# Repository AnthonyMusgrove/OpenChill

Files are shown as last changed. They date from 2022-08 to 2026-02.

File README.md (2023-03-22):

# OpenChill
OpenChill

OpenChill is an open source laser chiller firmware and hardware project using readily available parts from JayCar (Australia)
NOTE: You can also now install OpenChill on an MKS Base v1.4 3D Printer Control Board.  

Updated March 22nd 2023, OpenChill can be installed directly on an ESP8266, wiring diagram & instructions link will be available shortly.  The gist of the implementation is to #define OPENCHILL_ESP8266, set wifi SSID and wifi PASSWORD on lines 183 and 184, and if you want the portal to appear on a static local IP address, you need to #define IS_STATIC_IP then set IP address in segments IP_0,1,2,3, DNS_0,1,2,3, GW_0,1,2,3, and SUBN_0,1,2,3 (lines 191 to 212). You can also change the portal from the default web port 80 by changing #define WEB_PORT 80 (on line 214).

The portal address is simply at http://portal_ip_address<:port (if not 80)> - this will open the basic portal with some simple ajax framework to retrieve the live statistics.   If you just want the JSON statistics feed for your own integrations (into your laser software, etc) simply open http://portal_ip_address<:port (if not 80)>/stats - you'll receive a response similar to:

<code>{"environment":{"temperature": "26.5","humidity": "88","dewpoint": "24.3"},"reservior_temperature":"25.5","fridge_status":"off", "override_status":"off"}</code>

## Why OpenChill?
<p>A Co2 laser tube requires water cooling to maintain power, longevity and safety of the equipment.  The issue is, if the water can't be kept cool enough, the laser starts to lose power and over time, degrades and becomes unusable quicker.</p>  
<p>Why can't we just pump icy cold water through it then using a fridge or freezer?  Well, great question, it turns out that condensation buildup on and inside the laser tube causes 'arcing' and 'shorting' which can be harmful or fatal to YOU, the operator, and your laser.</p><p>  This is where OpenChill comes into play.</p>
<br/>
<p>OpenChill monitors the room's Humidity and Temperature using a sensor connected to the control board.  It then calculates the room's "dew point", which is the temperature in which the tubing will begin to generate condensation. </p><p> The firmware allows you to configure various settings (via wifi/web browser, and eventually a windows app), such as 'Set temperature of chiller dynamic to 3 degrees celsius ABOVE dew point', etcetera.  It will allow for remote monitoring and configuration, and eventually a touch screen, mounts, and more. It will also incorporate the K40 laser 'Cooler Warning' signal wire to shut the laser down incase certain conditions are met.</p>
<br/>
<p>The sky is truly the limit with OpenChill and I can't wait to see the progress over time of this awesome project.</p>
<br/>
<p>Images, instructions, firmware, etc all in progress of ALPHA, once ready for initial commit we can begin group collaboration.</p>

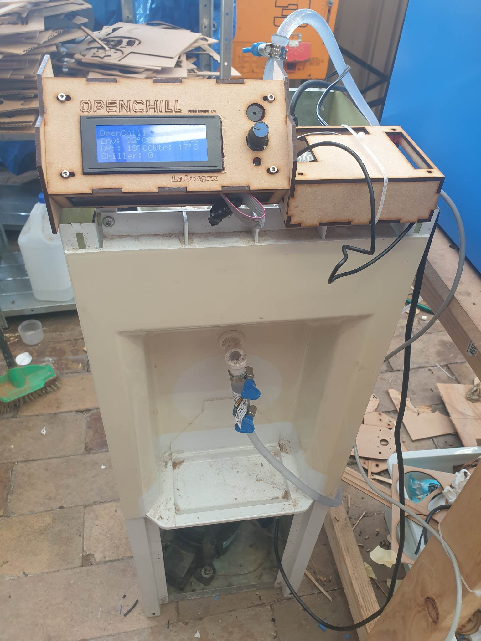
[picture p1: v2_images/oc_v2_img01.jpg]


## Parts List

Please see the BOM and Schematics PDFs -- parts won't be listed here anymore, only in the files.  All parts available from Jaycar Australia

## Non standard bits and pieces

* A water cooler with a working condensor/fridge mechanism.  We will be removing the thermostat that it has and installing OpenChill. 

## Downloads 
* OpenChill Uno Firmware
* OpenChill ESP Firmware
* OpenChill Windows Monitoring Tool
* OpenChill Enclosure Lasercut Files 

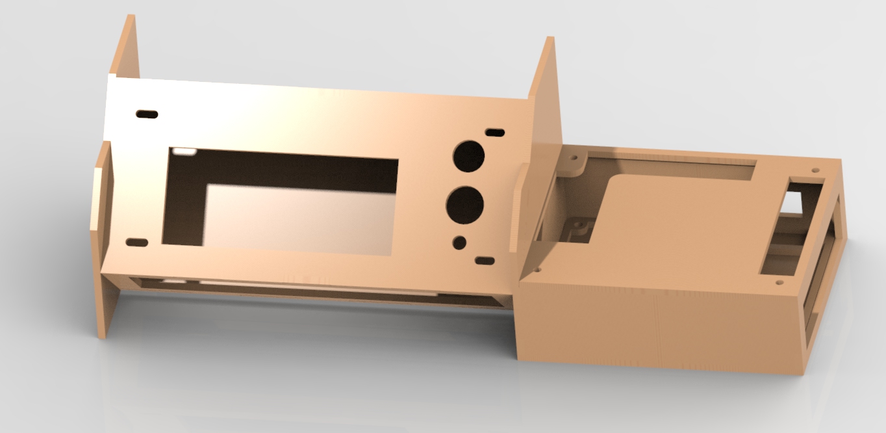
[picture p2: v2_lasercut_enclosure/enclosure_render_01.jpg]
EnclosureRender


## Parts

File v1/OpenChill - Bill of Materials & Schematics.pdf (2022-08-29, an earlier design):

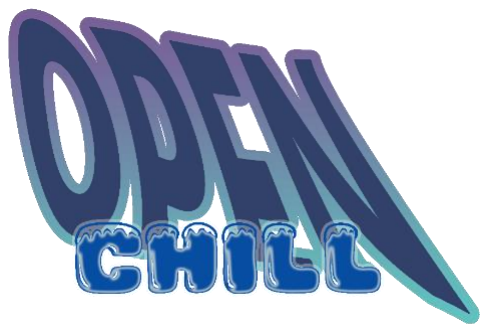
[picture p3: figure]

## Bill of Materials & Schematics

## Ver 1.0.0

## All part numbers refer to Jaycar Part Numbers in Australia; more info: jaycar.com.au

## Anthony Musgrove

## 30th August 2022

## BILL OF MATERIALS

QTY | Part# | Description | Notes
1 | XC4411 | Uno with Wi-Fi | You can substitute this part with a standard Arduino Uno if you don’t want the web portal and remote monitoring
1 | XC4424 | Buzzer Module
1 | XC4520 | Temperature and Humidity Sensor Module
1 | XC4419 | 5V Relay Module
1 | SY4040 | Heavy Duty Chassis Mount 10A /250VAC Relay | https://www.jaycar.com.au/heavy-duty-chassis-mount-relays-30a/p/SY4040
1 | RP7504 | 1k Ohm Linear (B) Single Gang 16mm Potentiometer
1 | RN3440 | 10k NTC Thermistor
1 | PS0524 | Bulkhead Male DC Power Connector
1 | XC4514 | DC Voltage Regulator | Set to 5v for 5v relay & arduino supply (when Arduino isn’t connected to a PC)
10 | HM5172 | 2 Way PCB Screw Terminal | Get spares, they’re useful for interfacing all the bits together

Extras & Notes

Heat shrink & silicone or some other method of waterproofing the 10k NTC Thermistor (it will sit in the chiller water reservoir to measure the chiller’s water temperature). I used some 2mm thick foam and cyanoacrylate (super glue) to make a small envelope around the wiring and thermistor.

The goal is to create a PCB layout and upload so that you can get one made, or make it yourself. This is in the process now, as I’ve now got the schematic and footprints into Altium designer.

The current firmware doesn’t yet utilise the wifi chip on the Uno board – but it will VERY soon. The firmware component for that chip is almost ready to release an alpha version.

Fridge Control Circuit

This is designed to replace the existing thermostat in the water chiller. On the water chillers I’ve looked at, they’re just a two wire thermostat module with two spade terminals. I recommend you getting an electrician to install the main relay (NOT the 5v relay) into the fridge to replace the thermostat – this is important for various reasons and I take absolutely no responsibility whatsoever for any injury, death, damage, or other liability, damage or outcome. You should consult a licenced and qualified electrician for any high voltage side modifications.

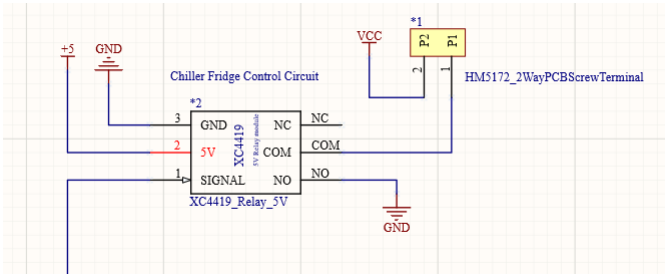
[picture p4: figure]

Signal wire above connects to Digital Pin 8 on the XC4411 Uno with Wi-Fi P1 and P2 need to go to the Fridge Main Relay (250v/10a relay) COIL terminals

Alarm Output Circuit

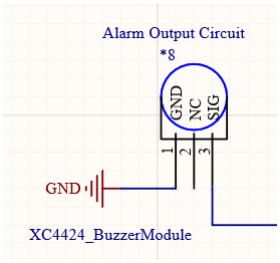
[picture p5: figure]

Pin 3 Signal wire connects to Digital Pin 10 on the XC4411 Uno with Wi-Fi

Environment Temperature & Humidity Input Circuit

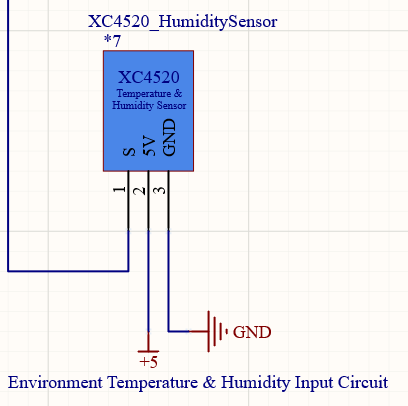
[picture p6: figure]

Pin 1 Signal wire connects to Digital Pin 9 on the XC4411 Uno with Wi-Fi

Chiller Water Temperature Input Circuit

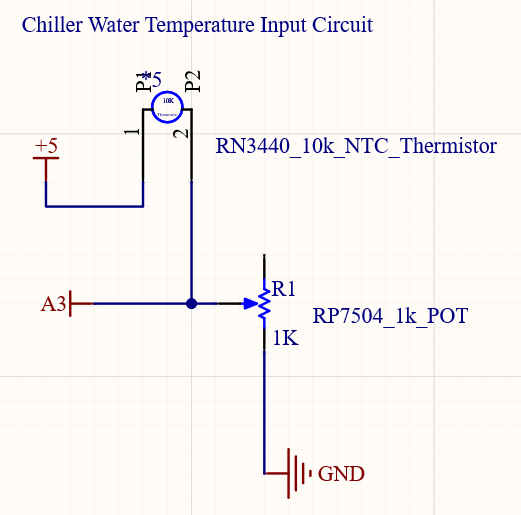
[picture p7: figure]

A3 wire connects to A3 (Analog Pin 3) on the XC4411 Uno with Wi-Fi

Power Supply Circuit

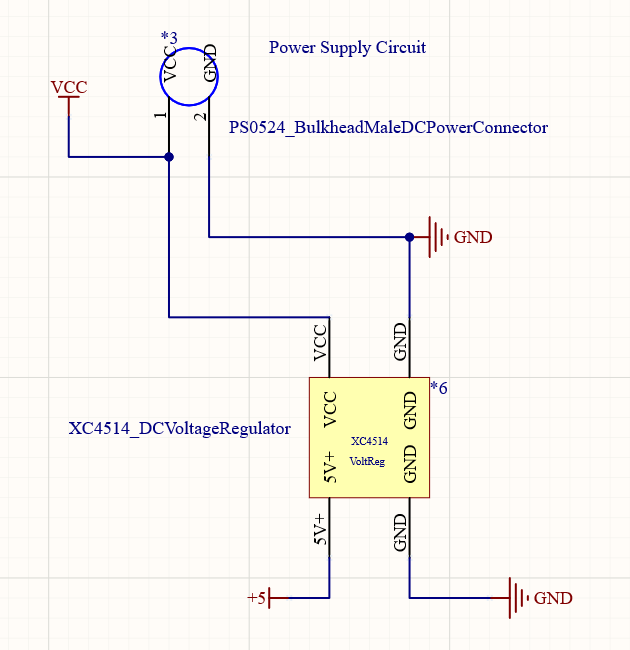
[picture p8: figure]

+5v can go to Arduino VIN to power the Arduino Uno. Make sure GND here is tied to Arduino GND as well. +5v also powers the 5v relay module, and again ensure GND is tied together with ALL grounds in the schematic.

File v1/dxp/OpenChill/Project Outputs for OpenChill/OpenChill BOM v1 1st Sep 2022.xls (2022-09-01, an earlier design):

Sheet: BOM Report
Bill of Materials |  |  | Bill of Materials for Project [OpenChill.PrjPcb] (No PCB Document Selected)
Source Data From: |  | OpenChill.PrjPcb
Project: |  | OpenChill.PrjPcb
Variant: |  | None
Creation Date: | 1/09/2022 | 1:59 PM
Print Date: | 2022-09-01 | 14:00:52
Footprint | Comment | LibRef | Designator | Description | Quantity
OpenChill_2xThruHole | HM5172_2WayPCBScrewTerminal | HM5172_2WayPCBScrewTerminal | *1, *4, *5 | [NoValue], LASER CUTOFF EMERGENCY, LASER ACTIVE | 3
XC4419_5VRelay_Footprint | XC4419_Relay_5V | XC4419_Relay_5V | *2 |  | 1
ARDUINO_INTERFACE_FOOTPRINT | UnoWithWifi | UnoWithWifi | *3 |  | 1
OpenChill_2xThruHole | PS0524_BulkheadMaleDCPowerConnector | PS0524_BulkheadMaleDCPowerConnector | *6 |  | 1
OpenChill_3xThruHole | XC4520_HumiditySensor | XC4520_HumiditySensor | *7 |  | 1
XC4424_BuzzerModule_Footprint | XC4424_BuzzerModule | XC4424_BuzzerModule | *8 |  | 1
OpenChill_2xThruHole | RN3440_10k_NTC_Thermistor | RN3440_10k_NTC_Thermistor | *9 |  | 1
XC4514_VoltReg_Footprint | XC4514_DCVoltageRegulator | XC4514_DCVoltageRegulator | *10 |  | 1
VR5 | RP8510_10k_POT | RPot | R1 | Potentiometer | 1
PARTS NOT LISTED IN SCHEMATIC
SY4040 Relay x1
 |  |  |  |  | 11
Approved |  | Notes

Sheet: Project Information
Project Full Path | C:\Users\Anthony\Documents\GitHub\OpenChill\dxp\OpenChill\OpenChill.PrjPcb
Project Filename | OpenChill.PrjPcb
Variant Name | None
Data-Source Filename | OpenChill.PrjPcb
Data-Source Full Path | C:\Users\Anthony\Documents\GitHub\OpenChill\dxp\OpenChill\OpenChill.PrjPcb
Title | Bill of Materials for Project [OpenChill.PrjPcb] (No PCB Document Selected)
Total Quantity | 11
Report Time | 1:59 PM
Report Date | 1/09/2022
Report Date & Tine | 1/09/2022 1:59 PM
Output Name | Bill of Materials
Output Type | BOM_PartType
Output Generator Name | BOM
Output Generator Description | Bill of Materials

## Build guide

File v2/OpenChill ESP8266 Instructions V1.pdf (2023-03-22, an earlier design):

# ESP8266 Instructions

Document version 1.0.0
Date Released 22/03/2023
Author Anthony Musgrove
Contact anthony@labworx.au

So you’ve heard the great news .. OpenChill can now be installed on a simple mini ESP8266. Well you’ve heard right. Despite the small footprint, the ESP8266 is actually quite a powerful unit, encapsulating WIFI! So the considerations when porting to ESP8266 were that this chip doesn’t have enough pins for an LCD screen with all our other stuff – not a problem, we eliminate that requirement by publishing a simple web portal over wifi so you can monitor OpenChill on your phone or computer, or connect the json data stream directly into compatible software that you can make do with it how you please.

At this stage, the firmware only provides a simple web portal, with statistics output – there’s no configuration changes, etc, so need not worry that it isn’t yet password protected. This can come later.

The other consideration we had to note was the fact that this chip is 3.3v level logic – which means it will NOT switch a 5 volt relay for the compressor – no big issues here though. By far the simplest and most elegant solution here would be to use a solid state relay such as the SSR40 (yeah yeah, 40 amps, a bit overkill Anthony), oh well, they’re cheap as chips – $8-$15 AUD will get you an SSR40 – which gives you the ability to switch up to 40 amps (yes, 40!) at 240volts AC, and will support a switching gate voltage of just 3 volts! Perfect …!

So lets get down to the nitty gritty – this document isn’t yet complete. It’ll be updated after I finish moving house!

Editing the firmware to support ESP8266

First step is to check that the firmware is correctly configured, _before_ you compile it. With the ESP8266, it is a requirement that you set the SSID and Password for your WIFI before compiling and flashing the firmware (at this stage anyway – later we can integrate the settings into the EEPROM and have them modifiable via the web portal – all will come in good time).

First step – define the board name #define OPENCHILL_ESP8266

(this is instead of any of the others, for example OPENCHILL_HARDWARE_V1 or MKS_BASE_1_0).

By defining the board type as OPENCHILL_ESP8266, the firmware will then include and compile the ESP8266 libraries, Wifi client, Webserver and DNS libraries). It will also define the CPU map (pinout wiring) as follows :-

D0 | Unused | Spare (for now)
D1 | Unused | Spare (for now)
D2 | Unused | Spare (for now)
D3 | Override Switch | Input Pullup, switch LOW to activate Override switch – this will keep the fridge compressor ON (or D4 -> HIGH) for as long as the switch is enabled.
D4 | Fridge/Compressor Relay | 3.3v output logic for the Solid State Relay gate
D5 | Buzzer/Audio | For alerts/alarms. If you don’t add a buzzer, no big deal – you just won’t hear it if it detects the reservoir temperature above the maximum allowed value
D6 | Safety Cutoff Signal | Not yet used – will be soon
D7 | Laser In Use Signal | Not yet used – will be soon
D8 | DHT11/22/etc Sensor Signal | The (S)ignal pin from your DHT11 or DHT22 sensor
A0 | Reservoir Temperature Signal | Analog Input pin for a temperature probe – I made my probe from a simple thermocouple in heatshrink then covered in foam. Depending on your thermocouple you use you may need to change the mapping code manually to support its range – we need to make this more versatile in the future

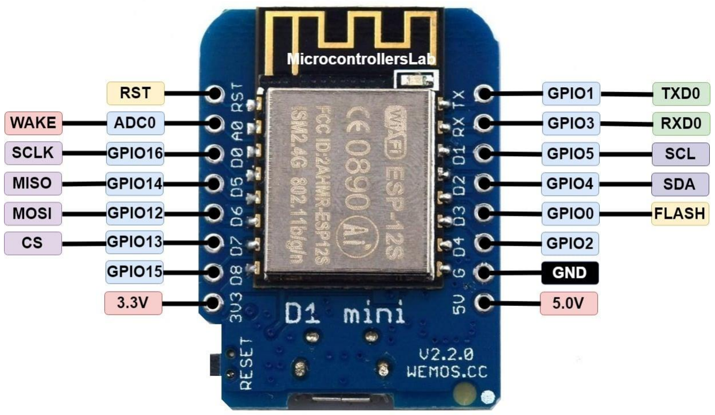
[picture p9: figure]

You need to configure your wifi SSID and PASSWORD. If you’re unsure of these values they may be on a sticker on your router.

Scroll down to line 183 (approx.) and configure the following lines :-

#define WIFI_SSID | "YourWIFISSIDHere"

#define WIFI_PASSWD | "YourWIFIPasswordHere"

Along with configuring the wifi SSID and PASSWORD – you can also specify a static lan IP address if you wish to have the web portal / json data stream open on the same IP address always – you can also override the default web port 80.

To set a static IP

Scroll down to line 186 (approx.) of the firmware and find the line

#define IS_STATIC_IP

Once you’ve told OpenChill firmware to use a static IP, you need to set the values from approx. line 191 to line 212. They include IP, DNS, Gateway and Subnet Mask, example shown below:

/* Portal IP Address (Example: 192.168.1.75) */
#define IP_0 192

#define IP_1 168

#define IP_2 1

#define IP_3 85

/* DNS IP Address (Example: 192.168.1.1) */ #define DNS_0 192
#define DNS_1 168

#define DNS_2 1

#define DNS_3 1

/* Gateway/Router Address (Example: 192.168.1.1) */ #define GW_0 192
#define GW_1 168

#define GW_2 1

#define GW_3 1

/* Subnet Mask (Example: 255.255.255.0) */ #define SUBN_0 255
#define SUBN_1 255

#define SUBN_2 255

#define SUBN_3 0

This will tell the firmware to publish the simple web portal on IP address 192.168.1.85, using DNS server 192.168.1.1, Gateway (or your wifi router address) 192.168.1.1, and a subnet mask of 255.255.255.0 – networking configuration is out of scope for this document – If you need to clarify any of these settings you need to either speak with your network administrator or read up on your router settings (and local area network settings). Who knows, we might do some more in depth tutorials on this stuff at a later stage.

Changing the default port for the portal

If you want to take the portal off the default web (http) port (80), you can modify the line (approx. 214):

#define WEB_PORT | 80

Once you’ve got your settings modified, compile the firmware using the Arduino IDE, while your ESP8266 is connected via USB (or however you wish to achieve programming your ESP8266).

When you boot it up, you should see a simple web portal on your portal address :

http://static_configured_ip:port

Note – if your port is left at default 80, you do not need to specify a port, simply http://ip_address/

Also note – if you did not choose to use a static IP address, you’ll need to locate the device on your local network by either IP scanning your net range, or checking ‘connected devices’ or the like on your wifi router/modem.

The simple portal appears somewhat like the following :-

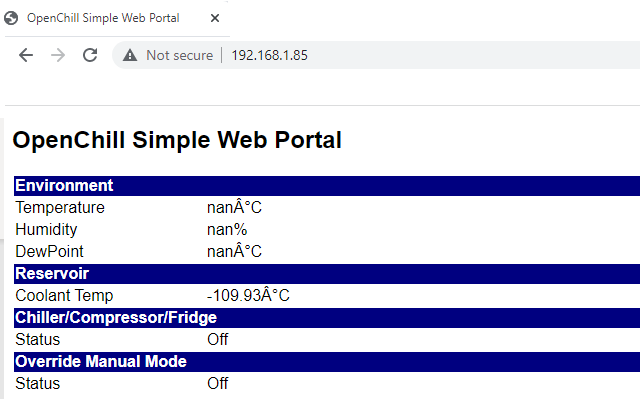
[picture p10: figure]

Environment Temperature and Humidity come from your DHT11/22 sensor. The dewpoint is calculated using the dewpoint formula (Td = T 0((100 -RH/5.) where Td is dew point temperature (in degrees Celsius), T is observed temperature (in degrees Celsius), and RH is relative humidity (in percent).

The values shown in my example above are what you’ll typically see without your DHT11/22 sensor connected (nan = Not A Number), and the firmware knows not to attempt to switch on the compressor if these invalid values are received).

Reservoir Coolant Temperature is the temperature value received by your temperature probe installed inside your chiller – remember this may be inaccurate and may need calibrating (and even some code changes to the mapping etc) – right now this isn’t very versatile so this is a massive TODO for the near future – to get some predefined sensor types and their mapping values into the firmware. For now though, use a BBQ probe or Meat probe and do some calculations to getting your particular sensor working correctly.

Chiller/Compressor/Fridge Status is the indicative value that your logic gate for your solid state relay is ON or OFF – and this subsequently will be what powers your compressor pump or whatever you choose to power with the solid state relay.

Override Manual Mode Status is the status of your manual override switch. If you choose to use a manual override switch – I added it as I found it handy when my temperature probe is inaccurate (because of calibration issues) and I really needed to get laser jobs done, I’d just flick it over to manual mode and monitor the temperature manually – however I rarely need this now as I’ve got my implementation configured/dialed in pretty well.

How do I just access the raw stats?

If you just want a JSON formatted feed of the vitals from openchill, such that you can connect it to your laser software or some other software that can use this data, etc, you can open the stats URL directly at:

http://openchill_ip_address/stats (if you changed your default web port from 80, you’ll also need to specify the port – ie: http://openchill_ip_address:port/stats).

You’ll be presented with the JSON formatted stats data which will appear like the following -:

{"environment":
{"temperature": "nan",
"humidity": "nan",
"dewpoint": "nan"},
"reservior_temperature":"-109.93", "fridge_status":"Off",
"override_status":"Off"}

When you have sensors connected and its working correctly, you’ll see values instead of nan (not a number) for temperature, humidity and dewpoint.

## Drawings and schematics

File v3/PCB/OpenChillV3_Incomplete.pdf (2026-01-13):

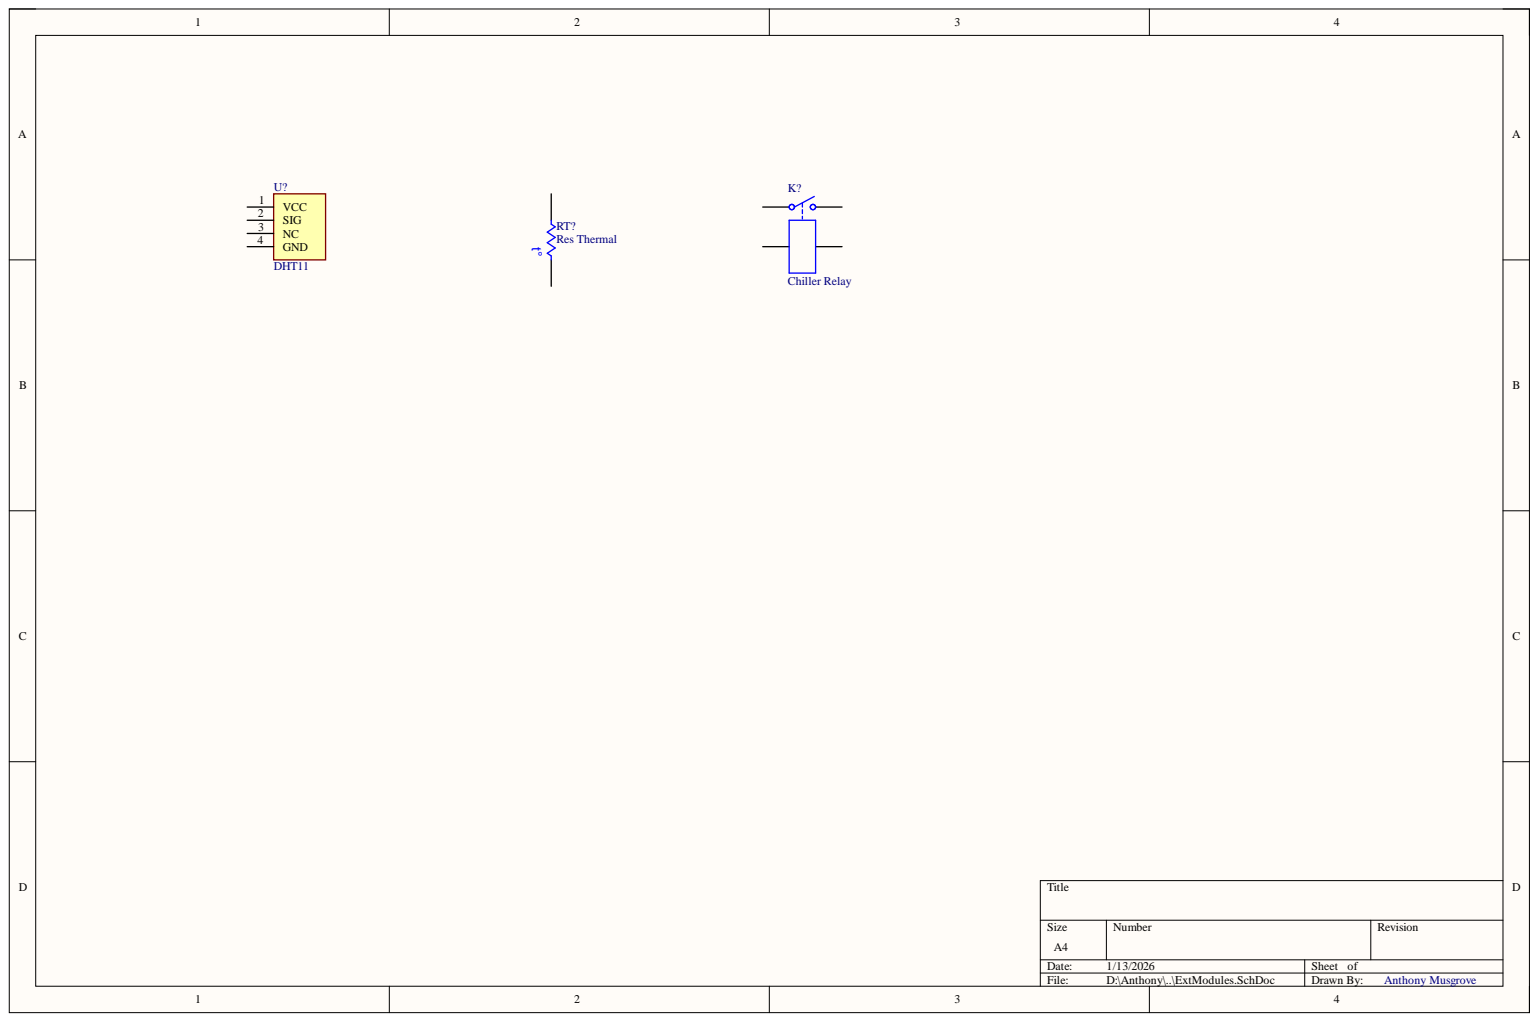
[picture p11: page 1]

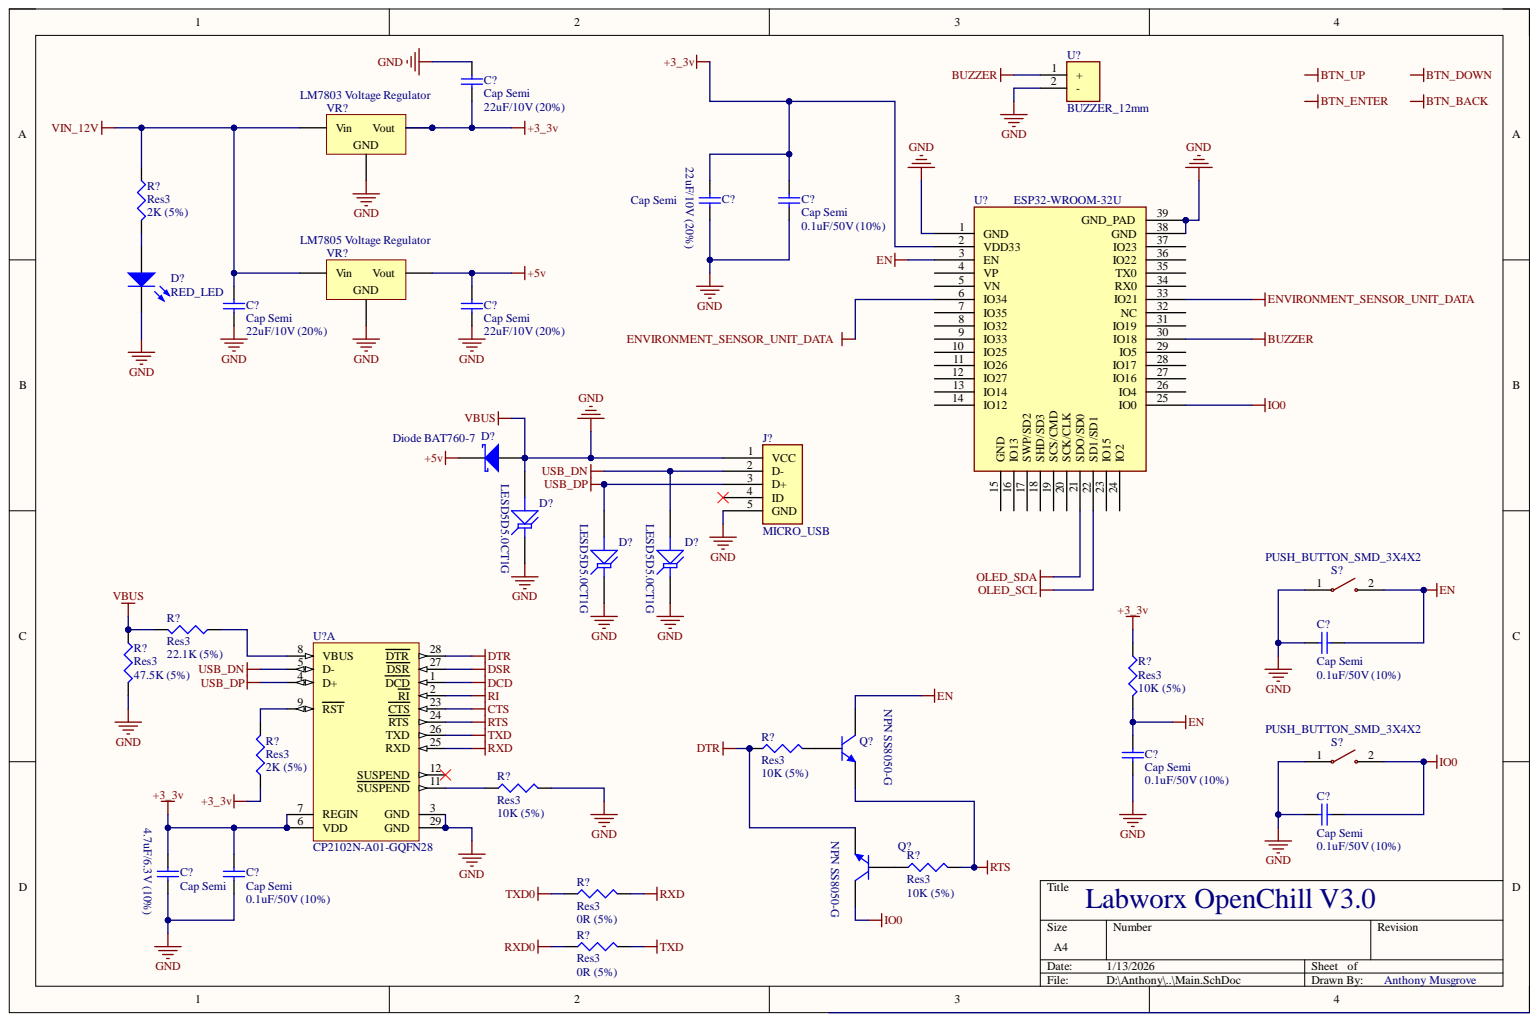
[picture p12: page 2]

D- 2
D+ 3

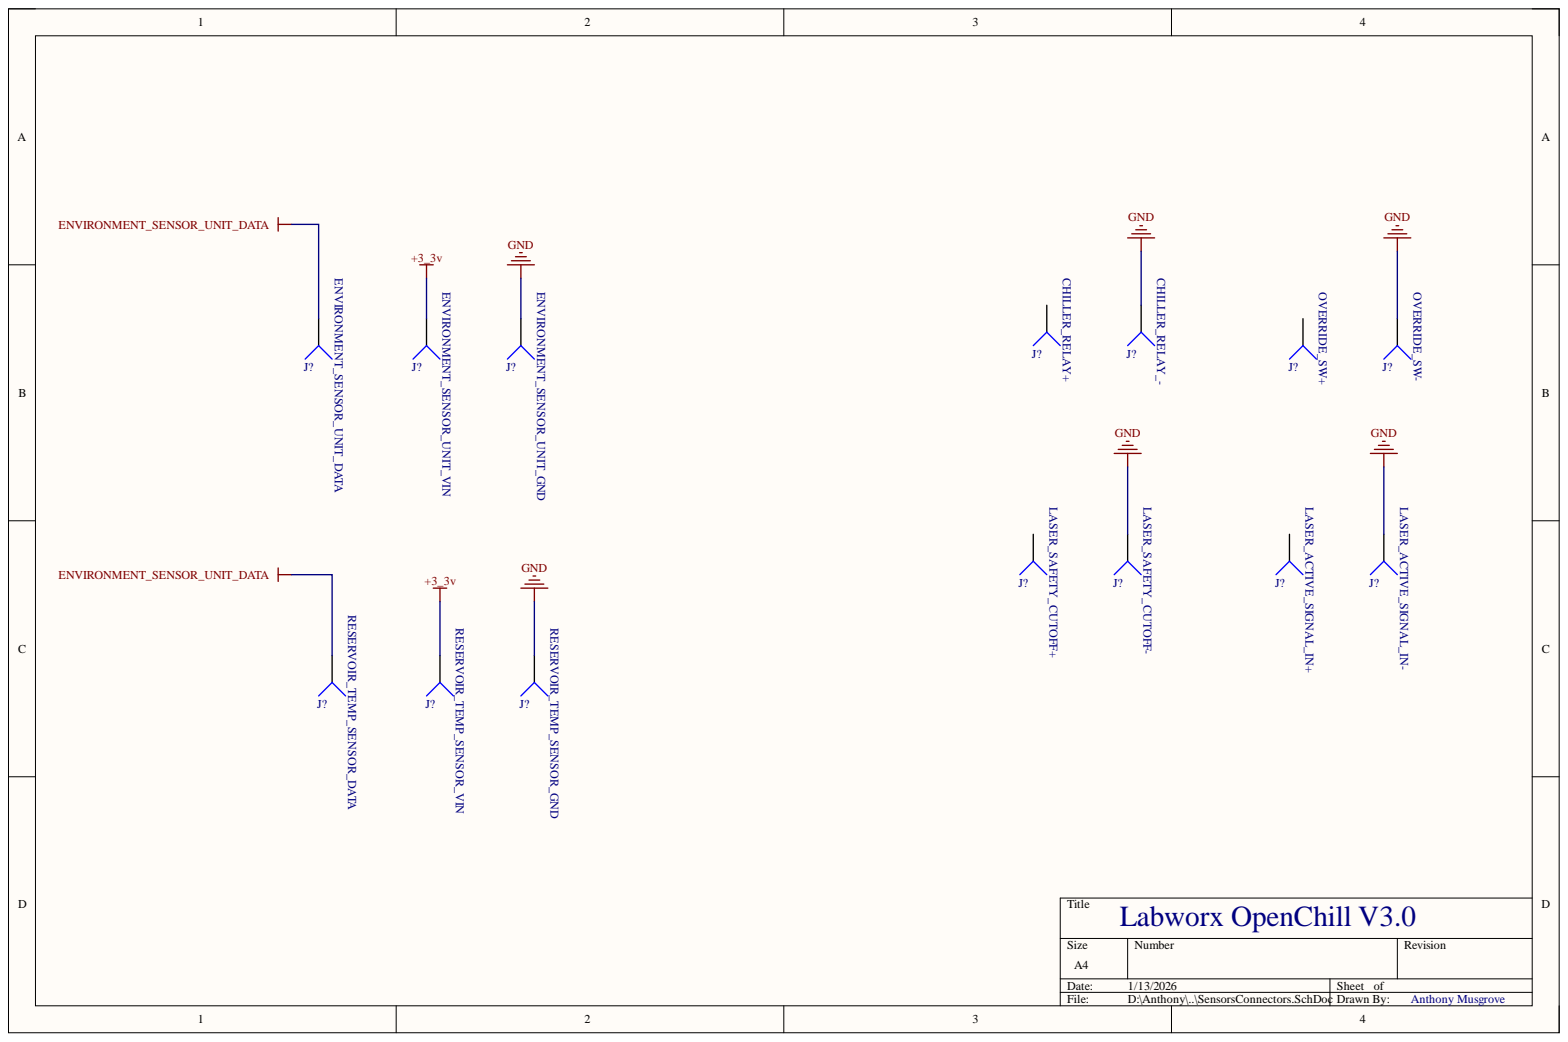
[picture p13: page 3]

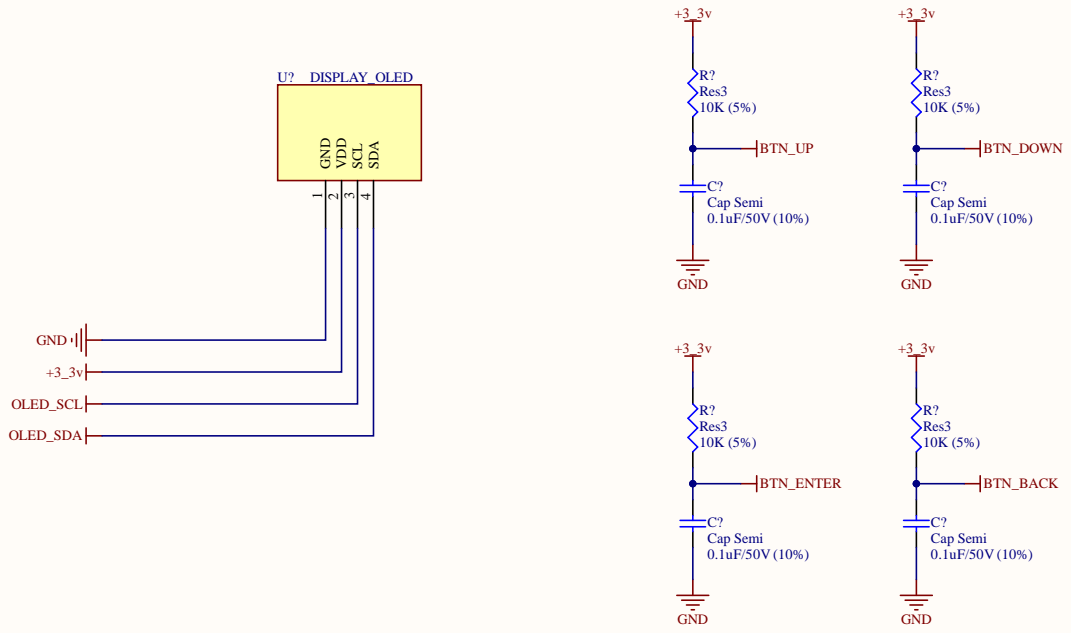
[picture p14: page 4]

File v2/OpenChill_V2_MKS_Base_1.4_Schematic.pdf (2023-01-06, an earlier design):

# 2.0 for MKS Base 1.4

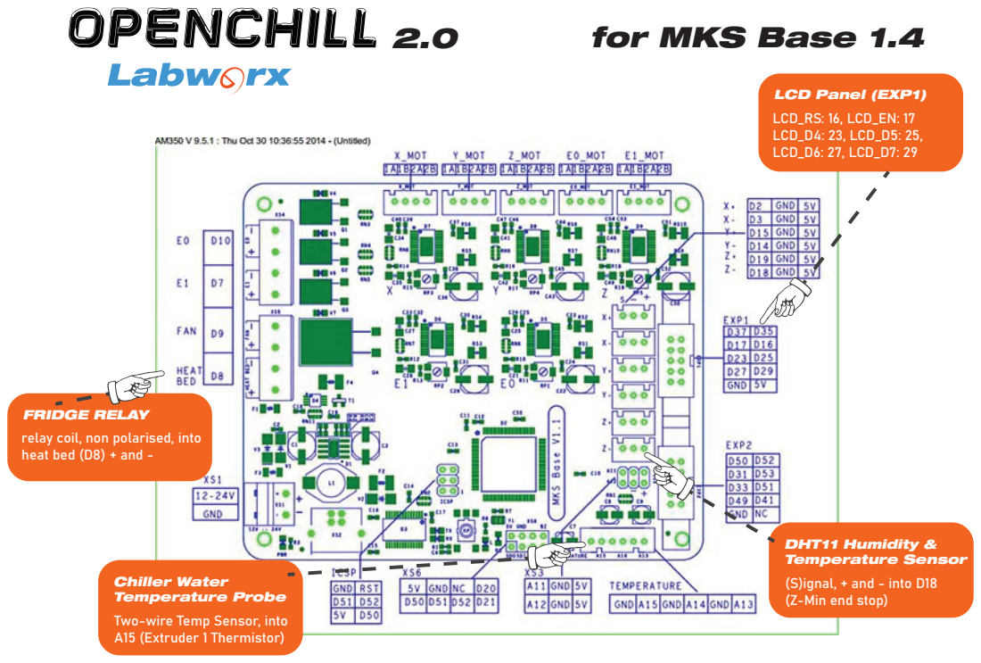
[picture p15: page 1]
LCD Panel (EXP1) LCD_RS: 16, LCD_EN: 17 LCD_D4: 23, LCD_D5: 25, LCD_D6: 27, LCD_D7: 29

FRIDGE RELAY
relay coil, non polarised, into
heat bed (D8) + and -

DHT11 Humidity &
Temperature Sensor
(S)ignal, + and - into D18
(Z-Min end stop)

Chiller Water
Temperature Probe
Two-wire Temp Sensor, into
A15 (Extruder 1 Thermistor)

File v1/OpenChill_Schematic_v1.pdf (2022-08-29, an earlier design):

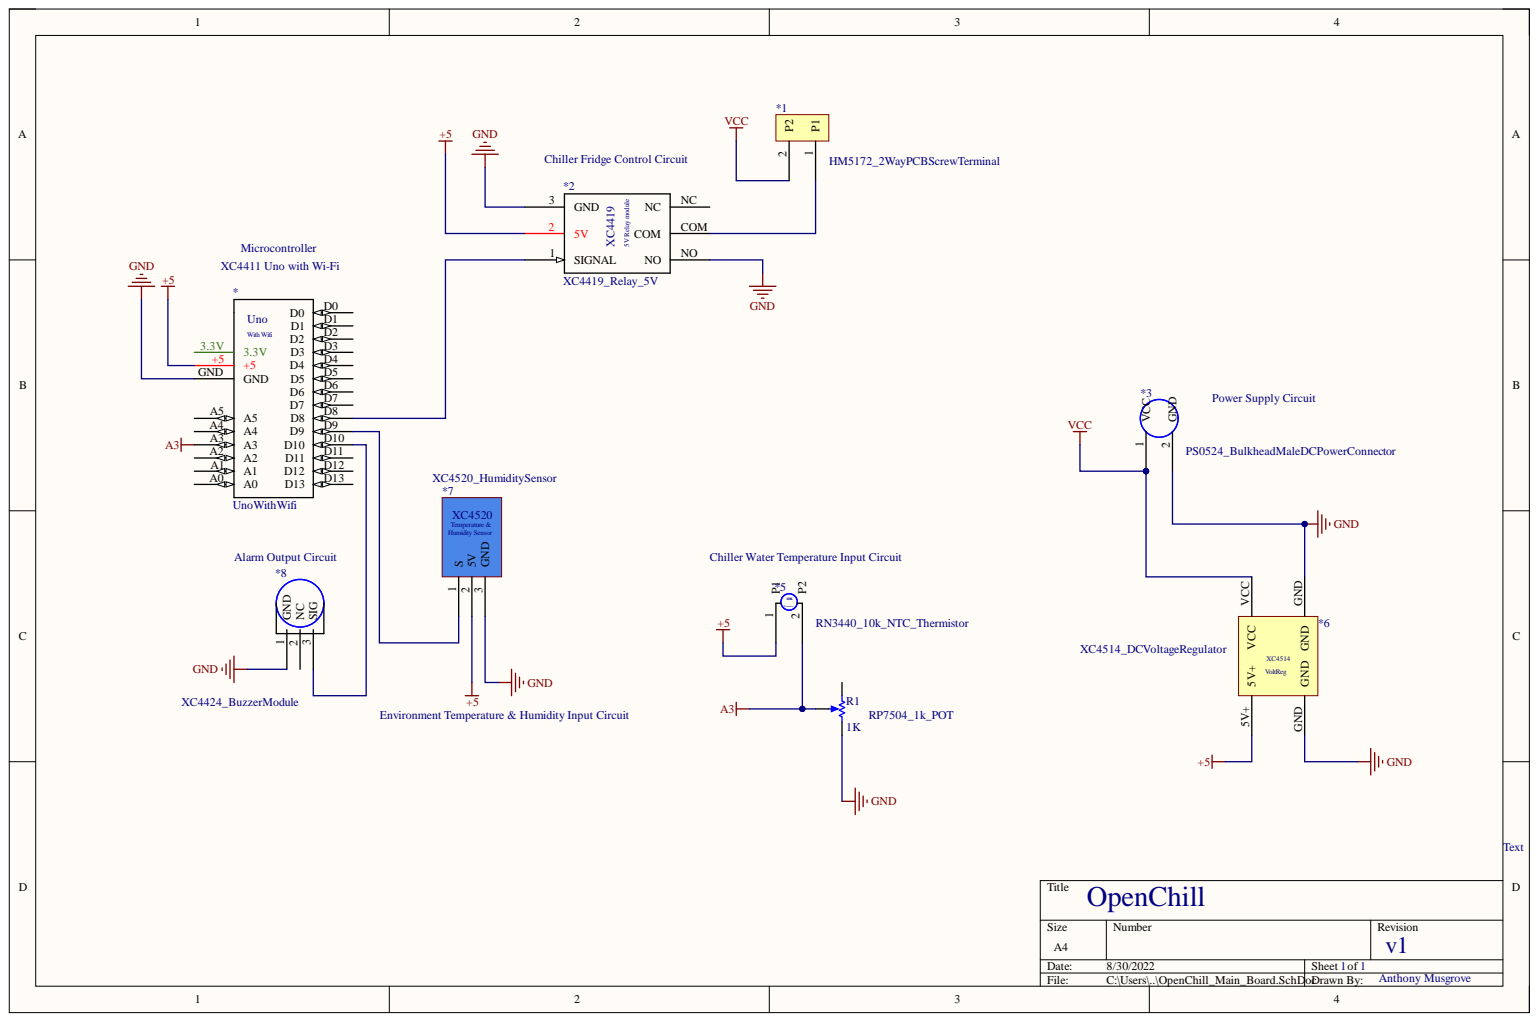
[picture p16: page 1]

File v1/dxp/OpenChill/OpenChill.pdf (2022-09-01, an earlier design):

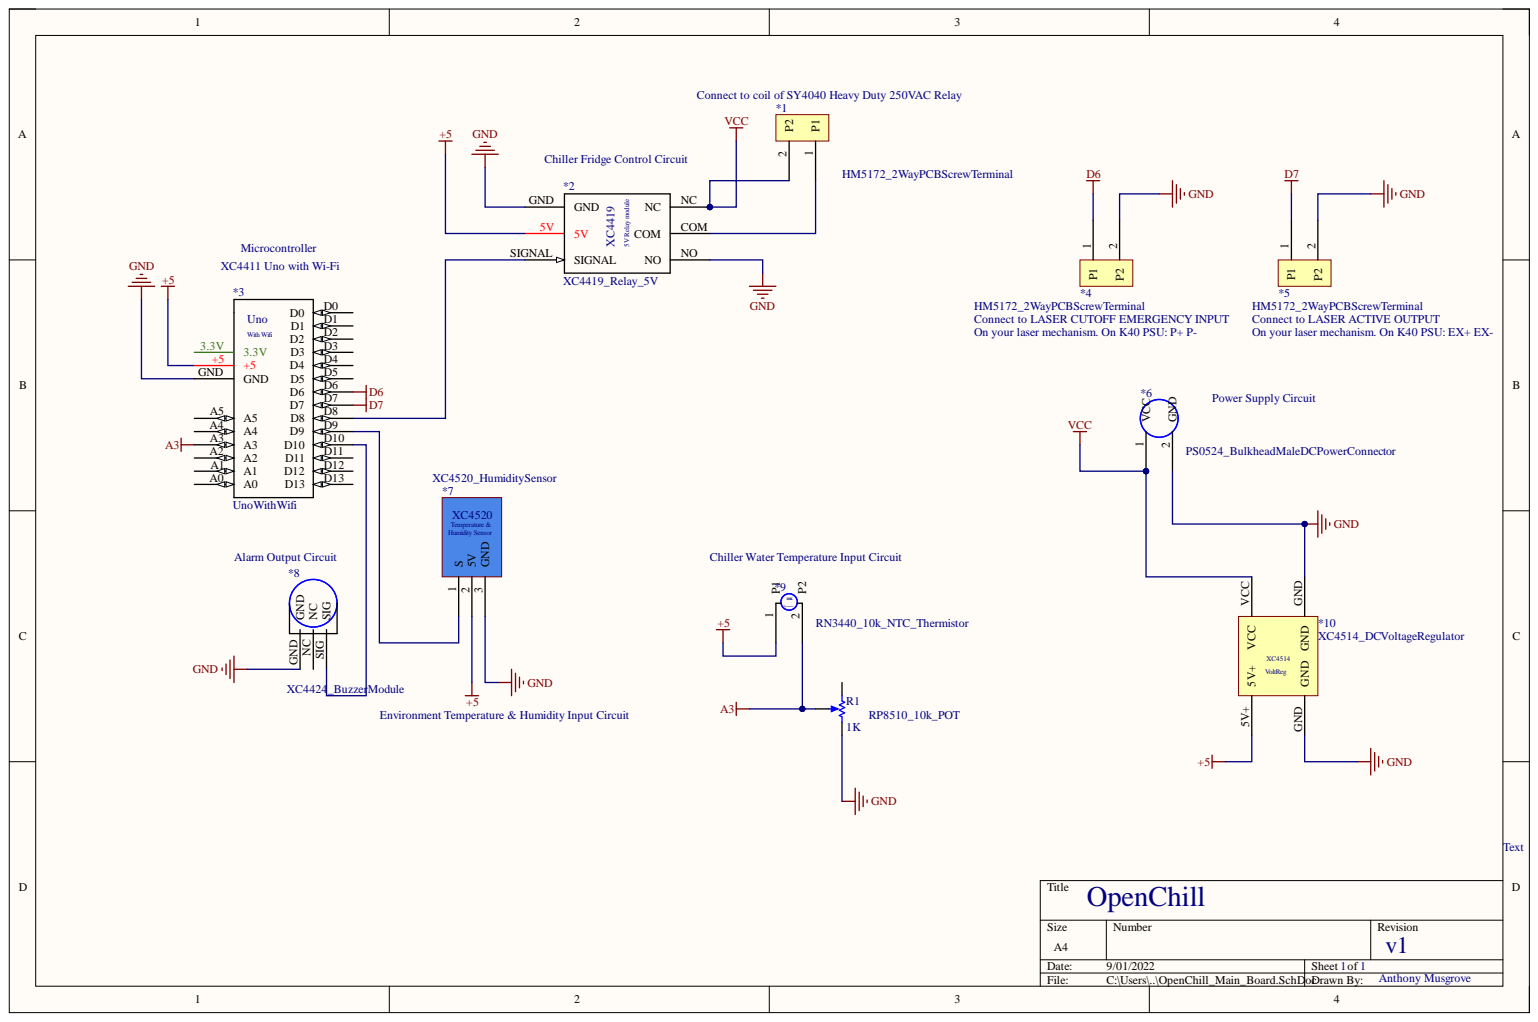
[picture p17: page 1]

D 1 2
D 1 3

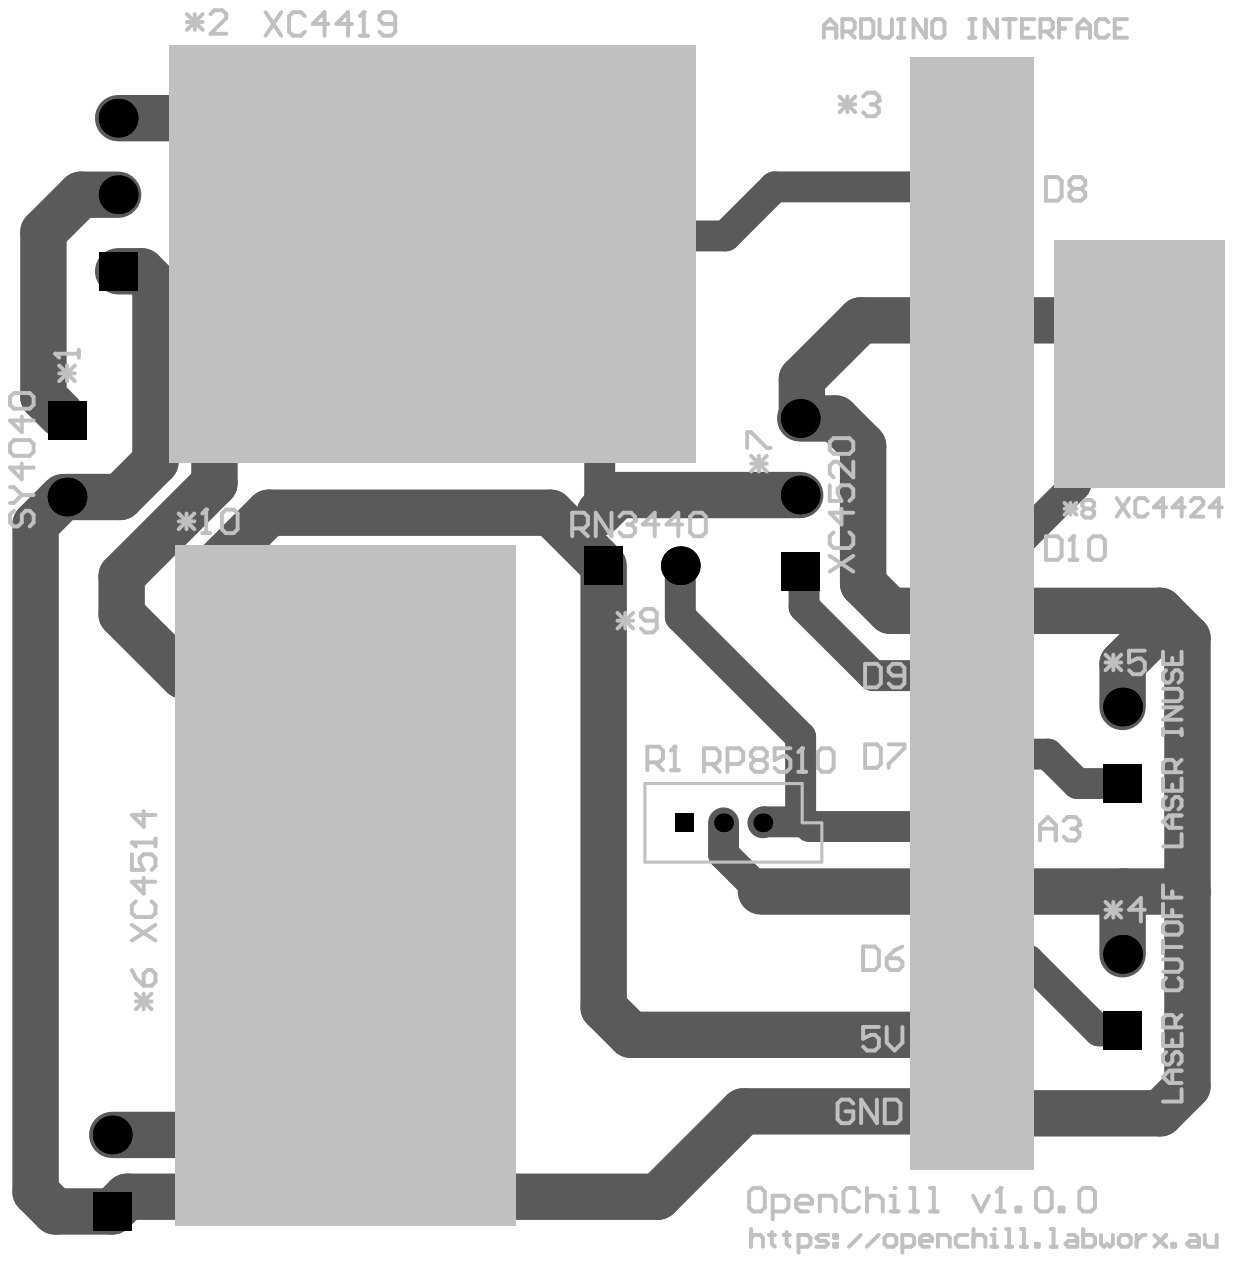
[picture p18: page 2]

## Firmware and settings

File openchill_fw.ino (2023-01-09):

/* 
 *    O P E N C H I L L
 *    Controller Firmware
 *    
 *    Contributors:
 *    Anthony Musgrove  (Project founder, since February 2022)  anthony@labworx.au
 *  
 *    OpenChill is an open source laser chiller firmware and hardware project using readily available parts from JayCar (Australia)
 */

  /*
   *  User Configuration - This data WILL EVENTUALLY be retrieved from the onboard ESP chip EEPROM, so eventually these
   *  variables will no longer be configurable here.
   */


   /* Ver 2.0.0 
   
      Released to the public January 6th, 2023.

      Major change:   #define MKS_BASE_1_4 to use OpenChill on an MKS Base 1.4 3D Printer Board (Extremely stable).  Not recommended at this stage to 
                      build OpenChill board (old version) as new version with much better layout and component choice will be available to the public
                      shortly.

                      Note:  If you have another 3D Printer board laying around that you'd like to see working with OpenChill, please send a ticket on GitHub
                             with the board details including any exact model numbers, brands etc, and a photo or image of the board in question.
   */

#include <LibPrintf.h>
#include <LiquidCrystal.h>

#define MKS_BASE_1_4



/*  OpenChill Hardware V1 CPU MAP */
#ifdef OPENCHILL_HARDWARE_V1
#define LCD_RS 12
#define LCD_EN  11
#define LCD_D4 5
#define LCD_D5 4
#define LCD_D6 3
#define LCD_D7 2

#define SAFETY_CUTOFF_SIGNAL_PIN 6 /* OUTPUT Signal wire for OpenChill to direct laser to cease operating  */
#define LASER_IN_USE_PIN 7 /* INPUT Signal wire from laser to advise OpenChill that laser is currently in use */
#define FRIDGE_RELAY_PIN 8 /* Arduino Digital Pin for the Fridge Relay Circuit */
#define DHT11_PIN 9   /* Arduino Digital Pin for the Signal Wire of the DHT11 Temperature & Humidity Sensor */
#define BUZZER_PIN 10 /* Arduino Digital PWM Piezzo/Buzzer Pin */
#define RESERVOIR_TEMP_PROBE_PIN A3  /* Arduino Analog Pin for the Chiller Temperature Probe Circuit Reading */

#endif

/*  MKS Base v1.4 CPU MAP */
#ifdef MKS_BASE_1_4
#define LCD_RS 16
#define LCD_EN  17
#define LCD_D4 23
#define LCD_D5 25
#define LCD_D6 27
#define LCD_D7 29

#define SAFETY_CUTOFF_SIGNAL_PIN 6 /* OUTPUT Signal wire for OpenChill to direct laser to cease operating  */
#define LASER_IN_USE_PIN 7 /* INPUT Signal wire from laser to advise OpenChill that laser is currently in use */
#define FRIDGE_RELAY_PIN 8 /* Arduino Digital Pin for the Fridge Relay Circuit */
#define DHT11_PIN 18   /* Arduino Digital Pin for the Signal Wire of the DHT11 Temperature & Humidity Sensor */
#define BUZZER_PIN 37 /* Arduino Digital PWM Piezzo/Buzzer Pin */
#define RESERVOIR_TEMP_PROBE_PIN A15  /* Arduino Analog Pin for the Chiller Temperature Probe Circuit Reading */

#endif

LiquidCrystal lcd(LCD_RS, LCD_EN, LCD_D4, LCD_D5, LCD_D6, LCD_D7);

// #define DEBUG
// OPTIONS:   DEBUG, DEBUGSERIAL, FRIDGECIRCUITDEBUG, SERIALMODE, PRODUCTION (production doesn't do anything yet)
#define DEBUG

 
 /* This value was used arbitrarily as my temperature probe on the MKS 1.4 board was always 8 degrees celsius higher than it should be.   
  * 
  * Calibration of the temperature probe using the MKS 1.4 board will be trial and error until I get some type of software calibration
  * working properly.  If your water temperature probe isn't accurate ( DO NOT SOLELY RELY ON THE MKS 4 TEMPERATURE PROBE WITHOUT CALIBRATING ),
  * submit a ticket so I can get some feedback on the best way to move forward with calibration.
 */
#define TEMP_CALIB_DIFF 8

#define DEGREES_ABOVE_DEWPOINT 1  /* OpenChill will aim to maintain a chiller temperature of x degrees ABOVE dewpoint */
#define MAX_TEMPERATURE_ALERT 26.5 /* Currently, OpenChill will emit an audible beep when chiller temperature exceeds this value */


/*  Instead of a single degree value for target above dewpoint, lets introduce a range.  For a few reasons - to stop the
 *   need for cutting in and out when the temperature fluctuates even by error, without having to introduce new code to
 *   detect and ignore (yet).  -anthony@labworx.au
*/

#define TARGET_TEMPERATURE_MIN_ABOVE_DEWPOINT 1
#define TARGET_TEMPERATURE_MAX_ABOVE_DEWPOINT 3



//#define DHTPIN 2

#define DHTTYPE DHT11   // DHT 11
//#define DHTTYPE DHT22   // DHT 22  (AM2302), AM2321
//#define DHTTYPE DHT21   // DHT 21 (AM2301)

#include "DHT.h"
DHT dht(DHT11_PIN, DHTTYPE);

//
/* variables to store the current DHT11 Temperature & Humidity reading, along with calculated Dew Point */
float currentEnvironmentTemperature;
float currentEnvironmentHumidity;
float currentEnvironmentDewPoint;

/* variables to store Chiller Reservoir Temperature & Analog Read value */
float currentReservoirTemperature = -9999; /* set to really icy cold low, so we can ensure not to act until atleast first sample is taken */
int currentReservoirVoltage;

#define WATER_TEMP_TOTAL_SAMPLES 50

/* variables to control rolling log of measurements for averaging */
float reservoir_temperature_log[WATER_TEMP_TOTAL_SAMPLES]; 
int cur_log_value = -1;

/* Keep track of Fridge circuit Status */
bool FridgeOn = false;


/* Setup Control Board */
void setup() {
  Serial.begin(115200);  /* Baud Rate MUST match Baud Rate of onboard ESP chip, tip:  Leave both set to 115200 */
  pinMode(BUZZER_PIN, OUTPUT); /* Define Buzzer Pin as an output */
  pinMode(FRIDGE_RELAY_PIN, OUTPUT); /* Define Fridge Relay Pin as an output */
  digitalWrite(FRIDGE_RELAY_PIN, LOW); /* Make sure initially we have the Fridge relay off */
  FridgeOn = false; /* Keep track of fridge circuit status, we've switched it off */

  pinMode(SAFETY_CUTOFF_SIGNAL_PIN, OUTPUT); /* OUTPUT Signal wire for OpenChill to direct laser to cease operating  */
  pinMode(LASER_IN_USE_PIN, INPUT); /* INPUT Signal wire from laser to advise OpenChill that laser is currently in use */

  lcd.begin(20, 4);
//  lcd.print("OpenChill.");
  dht.begin();

  setup_lcd();

}

 

void setEnvironmentAlert()
{

  //TODO:  Define a config flag for whether or not to send signal to laser to pause on alert(s)
  // Pin defined as SAFETY_CUTOFF_SIGNAL_PIN (digital pin 6)
    
  if(currentReservoirTemperature > MAX_TEMPERATURE_ALERT)
  {
    tone(BUZZER_PIN, 1000);
    delay(1000);
    noTone(BUZZER_PIN);
    delay(500);
  }
}

/*

  In the very near future this function is going to be rewritten with debouncing/idle time in mind, also
  instead of taking and acting on every temperature reading, it will be an average over x readings, so that
  the noise will be filtered out better.
*/

void setFridgeStatus()
{
/*
 * #define TARGET_TEMPERATURE_MIN_ABOVE_DEWPOINT 1
#define TARGET_TEMPERATURE_MAX_ABOVE_DEWPOINT 5
 */

  /*
   * Check current temperature is between min and max target, if its between the range, fridge goes off if its on..

    if its between the range and fridge is off, leave it off

    if its below the range, definitely off.

    if its above range, definitely on
   */

   if(currentReservoirTemperature < -9998)
   {
    #ifdef DEBUG
        Serial.println("Waiting for first water temperature sample before calculating fridge conditions ..");
    #endif

     return;
   }

  float min_target_temperature = currentEnvironmentDewPoint + TARGET_TEMPERATURE_MIN_ABOVE_DEWPOINT;  //  eg  dp=11, min above=1, min temp = 12
  float max_target_temperature = currentEnvironmentDewPoint + TARGET_TEMPERATURE_MAX_ABOVE_DEWPOINT;  //  eg  dp=11, max above=5, max temp = 16
  
  // check if current temperature is above min, but below max..
 if((currentReservoirTemperature >= min_target_temperature) && (currentReservoirTemperature <= max_target_temperature))
 {
   //if its in range, fridge can be turned off if its on
   if(FridgeOn)
   {
    
    #ifndef PRODUCTION
          Serial.println("Temperature in target range, fridge is on, so switching it off ..");
    #endif
          //fridge off
          digitalWrite(FRIDGE_RELAY_PIN, LOW);
          FridgeOn = false;
       }
       
       return;
     }
     else if(currentReservoirTemperature > max_target_temperature)
     {
    
    #ifdef DEBUG
        Serial.println("Temperature is above maximum target, switching fridge on ..");
    #endif
    
        //fridge on
        digitalWrite(FRIDGE_RELAY_PIN, HIGH);
        FridgeOn = true;
     }
     else if(currentReservoirTemperature < min_target_temperature)
     {

    #ifdef DEBUG
        Serial.println("Temperature is below minimum target, switching fridge off ..");
    #endif
    
        //fridge off
        digitalWrite(FRIDGE_RELAY_PIN, LOW);
        FridgeOn = false;
     }
     else
     {

      #ifdef DEBUG
        Serial.println("Condition met, but unknown yet why.");
      #endif
        //do nothing (yet) 
     }
}

void readReservoirProbeTemperature()
{
  currentReservoirVoltage = analogRead(RESERVOIR_TEMP_PROBE_PIN);

/*
 variables to control rolling log of measurements for averaging 
float reservoir_temperature_log[10] = {0, 0, 0, 0, 0, 0, 0, 0, 0, 0}; 
int cur_log_value = -1;
*/
  cur_log_value++;
  
  #ifdef MKS_BASE_1_4

    reservoir_temperature_log[cur_log_value] = map(currentReservoirVoltage, 1023, 0, -50, 50) - TEMP_CALIB_DIFF;

  #else
	  
	  float R1 = 10000;
	  float logR2, R2, T;
	  float c1 = 1.009249522e-03, c2 = 2.378405444e-04, c3 = 2.019202697e-07;

	  R2 = R1 * (1023.0 / (float)currentReservoirVoltage - 1.0);
	  logR2 = log(R2);
	  T = (1.0 / (c1 + c2*logR2 + c3*logR2*logR2*logR2));
	  T = T - 273.15;
	  T = (T * 9.0)/ 5.0 + 32.0; 

	  /* set Current Reservoir Temperature to current temperature in Celsius */
	  //currentReservoirTemperature = T;

    reservoir_temperature_log[cur_log_value] = T;

  #endif

  float total_for_avg = 0;

  if(cur_log_value == WATER_TEMP_TOTAL_SAMPLES)
  {
    for(int x=0; x< WATER_TEMP_TOTAL_SAMPLES; x++)
    {
        total_for_avg += reservoir_temperature_log[x];
    }

    currentReservoirTemperature = total_for_avg / WATER_TEMP_TOTAL_SAMPLES;
    cur_log_value = -1;
  }

}

void readEnvironment()
{
//  int chk = DHT.read11(DHT11_PIN);
  dht.read();
  currentEnvironmentHumidity = dht.readHumidity();        //  read humitity as %f
  currentEnvironmentTemperature = dht.readTemperature();     //  read temperature as Celsius (default)
  currentEnvironmentDewPoint = (currentEnvironmentTemperature - (100 - currentEnvironmentHumidity) / 5);
}

void debug_Out(bool fridge_test_mode)
{
  Serial.print("Total Samples: ");
  Serial.print(cur_log_value);
  Serial.print(" | Temp: ");
  Serial.print(currentEnvironmentTemperature);
  Serial.print(" | Humid: ");
  Serial.print(currentEnvironmentHumidity);
  Serial.print(" | Dew Point: ");
  Serial.print(currentEnvironmentDewPoint);
  Serial.print(" | Reservoir Temp: ");
  Serial.print(currentReservoirTemperature);
  Serial.print(" | Fridge Status: ");

  if(fridge_test_mode)
  {
    Serial.print(FridgeOn);
    Serial.println(" [Fridge Circuit Debug Active]");
  }
  else
  {
    Serial.println(FridgeOn);
  }
  
}

void serialMon_Update()
{
  Serial.print("|T:");
  Serial.print(currentEnvironmentTemperature);
  Serial.print(",H:");
  Serial.print(currentEnvironmentHumidity);
  Serial.print(",D:");
  Serial.print(currentEnvironmentDewPoint);
  Serial.print(",R:");
  Serial.print(currentReservoirTemperature);
  Serial.print(",F:");
  Serial.print(FridgeOn);
  Serial.print(",");
  Serial.println("^");

  // Output example:  |T:16.00,H:63.00,DP:5.00,RT:11.75,FR:0 or 1 (fridge compressor circuit on or off)^
  
}

void fridge_relay_debug()
{

  if(FridgeOn)
  {
    digitalWrite(FRIDGE_RELAY_PIN, LOW);
    FridgeOn = false;
  }
  else
  {
    digitalWrite(FRIDGE_RELAY_PIN, HIGH);
    FridgeOn = true;
  }

  delay(1500);
}

void setup_lcd()
{
  lcd.clear();
  lcd.setCursor(0, 0);
  lcd.print("OpenChill System v2");

  lcd.setCursor(0, 1);
  lcd.print("Env:");

  //update environment temperature
  lcd.setCursor(5,1);
  lcd.print("??");
  lcd.print((char)223);
  lcd.print("C");

  lcd.setCursor(10, 1);
  lcd.print("Hum:");

  //update humidity
  lcd.setCursor(15, 1);
  lcd.print("??%");
  
  lcd.setCursor(0,2);
  lcd.print("DPt:");

  //update dewpoint
  lcd.setCursor(5,2);
  lcd.print("??");
  lcd.print((char)223);
  lcd.print("C");

  lcd.setCursor(10,2);

  lcd.print("Wtr:");

  //update water/reservior temperature
  lcd.setCursor(15,2);
  lcd.print("??");
  lcd.print((char)223);
  lcd.print("C");

  lcd.setCursor(0,3);
  lcd.print("Chiller: ");

  //update fridge/chiller status
  lcd.setCursor(9,3);
  lcd.print("??");


}

void update_lcd()
{

  //update environment temperature
  lcd.setCursor(5,1);

  if(!isnan(currentEnvironmentTemperature))
  {
    lcd.print(currentEnvironmentTemperature,0);
  }
  else
  {
    lcd.print("!?");
  }

  lcd.print((char)223);
  lcd.print("C");

  //update humidity
  lcd.setCursor(15, 1);

  if(!isnan(currentEnvironmentHumidity))
  {
    lcd.print(currentEnvironmentHumidity,0);
  }
  else
  {
    lcd.print("!?");
  }

  lcd.print("%");
  
  //update dewpoint
  lcd.setCursor(5,2);

  if(!isnan(currentEnvironmentDewPoint))
  {
   lcd.print(currentEnvironmentDewPoint,0);
  }
  else
  {
    lcd.print("!?");
  }
  
  lcd.print((char)223);
  lcd.print("C");

  //update water/reservior temperature
  lcd.setCursor(15,2);

  if(currentReservoirTemperature > -9999)
  {
    lcd.print(currentReservoirTemperature,0);
    lcd.print((char)223);
    lcd.print("C");
  }
  else
  {
    lcd.print("**");
    lcd.print((char)223);
    lcd.print("C");
     
  }

  lcd.setCursor(9,3);
  lcd.print(FridgeOn);
/*
  Serial.print("|T:");
  Serial.print(currentEnvironmentTemperature);
  Serial.print(",H:");
  Serial.print(currentEnvironmentHumidity);
  Serial.print(",D:");
  Serial.print(currentEnvironmentDewPoint);
  Serial.print(",R:");
  Serial.print(currentReservoirTemperature);
  Serial.print(",F:");
  Serial.print(FridgeOn);
  Serial.print(",");
  Serial.println("^");
  */

}

/* Control Board Heartbeat */
void loop () 
{
//  lcd.setCursor(0, 1);
  // print the number of seconds since reset:
//  lcd.print(millis() / 1000);
  
  readEnvironment();   /* Read Environment */
  readReservoirProbeTemperature(); /* Read Reservoir Temperature */

#ifndef FRIDGECIRCUITDEBUG
  setFridgeStatus(); /* Set Fridge Status on or off based on above data */
#endif

  setEnvironmentAlert(); /* Create any alerts based on environment data, such as max chiller temp reached */


#ifdef DEBUGSERIAL
  tmp_increment_counter();
#endif

#ifdef DEBUG
  debug_Out(false);
#endif

#ifdef FRIDGECIRCUITDEBUG
  fridge_relay_debug();
  debug_Out(true);
#endif

#ifdef SERIALMODE
  serialMon_Update();
#endif

#ifdef PRODUCTION
#endif

  update_lcd();

  delay(250);

}

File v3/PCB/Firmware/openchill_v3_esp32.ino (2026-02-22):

/*  OpenChill V3.0 Firmware 

    Required Hardware
    =================


    1 x  ESP32 Dev Module (or the official PCB & Bill of Materials [still being developed, use an ESP32 Dev Module for simplicity])

    1 x  OLED Display; this firmware uses the SSD1306  128x64 OLED display, they're plentiful on ebay.  Its the 4-wire OLED screen (SCL,SCA,3.3V,GND)

    1 x Solid State Relay that can switch on/off with minimum 3VDC (eg, the GEYA Solid State Relay Module SSR-10A) which can switch on and off using 3-32 VDC, and can switch 24-480 VAC
        (I'll list this item in the documentation on GITHUB, you can select any relay provided that it has the same electrical properties)

    1 x DHT11 Module (Temperature & Humidity Sensor)

    1 x Temperature Sensor Module (I'm using a Jaycar XC4494, but any analog thermistor sensor which changes resistance with temperature)

    1 x Potentiometer (and knob, because can be used to calibrate the water reservior temperature, eventually this will be completely digital)

    1 x Vero board (just something to attach connectors to that can be cut to fit into the slots in the 3d printed case, this is for the plugin sockets etc)

    Some sockets / plugs (TBA after 3d printed case is completed)

    1 x full 3d printed OpenChill V3.0 case

*/

#include <SPI.h>
#include <Wire.h>
#include <Adafruit_GFX.h>
#include <Adafruit_SSD1306.h>


#define SCREEN_WIDTH 128 // OLED display width, in pixels
#define SCREEN_HEIGHT 64 // OLED display height, in pixels
#define OLED_RESET     -1 // Reset pin # (or -1 if sharing Arduino reset pin)
#define SCREEN_ADDRESS 0x3C ///< See datasheet for Address; 0x3D for 128x64, 0x3C for 128x32


Adafruit_SSD1306 display(SCREEN_WIDTH, SCREEN_HEIGHT, &Wire, OLED_RESET);


void setup() {

  Serial.begin(9600);
  delay(500);
  while (!Serial);

  Serial.println("OpenChill V3.0 DBG Serial");

  Serial.println("Initialising OLED Display ...");

  if(!display.begin(SSD1306_SWITCHCAPVCC, SCREEN_ADDRESS)) {
    Serial.println(F("SSD1306 allocation failed"));
    for(;;); // Don't proceed, loop forever
  }

  display.display();
  delay(2000); // Pause for 2 seconds

  // Clear the buffer
  display.clearDisplay();

  display.setTextSize(1);      // Normal 1:1 pixel scale
  display.setTextColor(SSD1306_WHITE); // Draw white text
  display.setCursor(0, 0);     // Start at top-left corner
  display.cp437(true);         // Use full 256 char 'Code Page 437' font

  display.println(F("OpenChill V3.0"));

  display.display();

}

void loop() {

}

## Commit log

2022-08-29 Schematic Ver 1
2022-08-29 Bill of Materials & Schematics
2022-08-30 add definitions for LASER_IN_USE_PIN and SAFETY_CUTOFF_SIGNAL_PIN
    These two pins are currently not functional, just definitions for now.
    Laser in use pin - signal from laser to advise openchill that the laser is currently running a job. On the K40 using Nano M2 board, this wire will connect to EX+, and a ground is tied from OpenChill 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
    SAFETY_CUTOFF_SIGNAL_PIN - this signal wire is to tell the laser that OpenChill needs it to pause/cease operation as OpenChill cannot achieve the desired chiller temperature, or needs a break to cool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
2022-09-01 Added DXP / Altium files
    Added PCB and Schematic files for DXP (Altium Designer)
    [OpenChill.PrjPcb, OpenChill_Components_Library.SchLib, OpenChill_Main_Board.SchDoc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]
2022-09-01 Modifications added for Emergency Cutoff & Laser Status, updated project URL & board layout
    [OpenChill.PrjPcb, OpenChill_Components_Library.SchLib, OpenChill_Main_Board.SchDoc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]
2022-09-01 Board layout changes
    Added Emergeny Cutoff plug and Laser status plug to board and modify layout slightly.
2022-09-01 Layout cont
    Board layout cont
    [OpenChill_PCB_01.PcbDoc]
2022-09-01 Added test all gerber export
    Added test all export gerber and board layout png for demo
    [OpenChill_PCB_01.GBL, OpenChill_PCB_01.GTL, OpenChill_PCB_01.GTO]
2022-09-01 Added demo of board layout (screenshot)
    cosmetic purposes only
2022-09-01 added gerber exports
    added bottom layer gerber (mirrored)
    added drill holes bottom (mirrored)
    [OpenChill BOM v1 1st Sep 2022.xls, OpenChill_PCB_01.PcbDoc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]
2023-01-06 V2 Upload
    V2 Upload - Allows MKS Board 1.4 to be used as controller board for openchill, please see schematics.
    [OpenChill BOM v1 1st Sep 2022.xls, OpenChill.PrjPcb, OpenChill_Components_Library.SchLib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]
2023-01-06 Added v2 enclosure lasercut files
    Added v2 enclosure lasercut files for MKS Base 1.4 board & reprap LCD controller - and a render of same.
2023-01-06 Moved Archive to v1
    Reflect V1 - moved Archive to V1
    [OpenChill BOM v1 1st Sep 2022.xls, OpenChill.PrjPcb, OpenChill_Components_Library.SchLib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]
2023-01-09 Added water temperature averaging
    Added water temp averaging to level out spikes, can define total samples.
    Also added some lcd output when values are nan (not a number) so that the end user knows something has gone wrong.
    [openchill_fw.ino]
2026-01-13 Initial push of V3 PCB Design
    Initial design files (Altium DXF) for PCB v3 Design 1
    [ExtModules.SchDoc, Main.SchDoc, OpenChill.PrjPcb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]
2026-01-14 Rectify SDA/SCL pins issue on V3
    SDA/SCL pins were incorrect, now tied to correct pins D21/D22
    [Main.SchDoc, SensorsConnectors.SchDoc, UserControlInterface.SchDoc]
